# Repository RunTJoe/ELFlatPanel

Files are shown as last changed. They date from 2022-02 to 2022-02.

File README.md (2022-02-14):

# DIY Electroluminescence Flatfield Panel

## Overview

Features:

- Software controlled brightness

- Motorized telescope cover

- "Alnitak Generic Commands" compatible protocol

- 3D printed enclosure

The panel is designed for my 120mm refractor. I have mounted a 160mm EL panel into a 3D printed telescope cover. A servo motor opens and closes the cover.

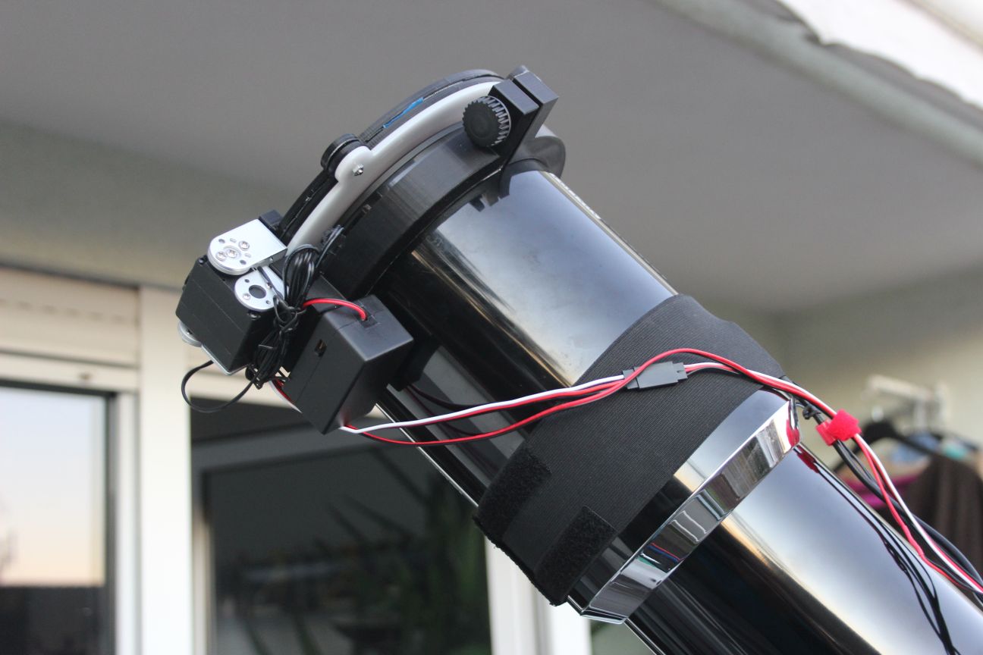
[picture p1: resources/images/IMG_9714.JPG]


Brightness and open/close operation are controlled by software using an "Alnitak Generic Commands" compatible protocol. This protocol is supported by several imaging software, I have tested operation in depth with imaging software "[Voyager](https://software.starkeeper.it/)" and briefly with "[N.I.N.A.](https://nighttime-imaging.eu/)".

Meanwhile I have successfully tested the panel for a whole night of unattended operation with temperatures below 0°C/ 32°F. During this night I shot multiple targets with different rotator angles and got the fitting flats for each rotator position. The imaging software automatically determined the correct brightness for luminance and narrowband filters and a fixed exposure time to fit my flatdark library.

## Panel

The panel is a cheap 160mm EL panel from Aliexpress. The controller is designed to be connected to a 12V inverter.

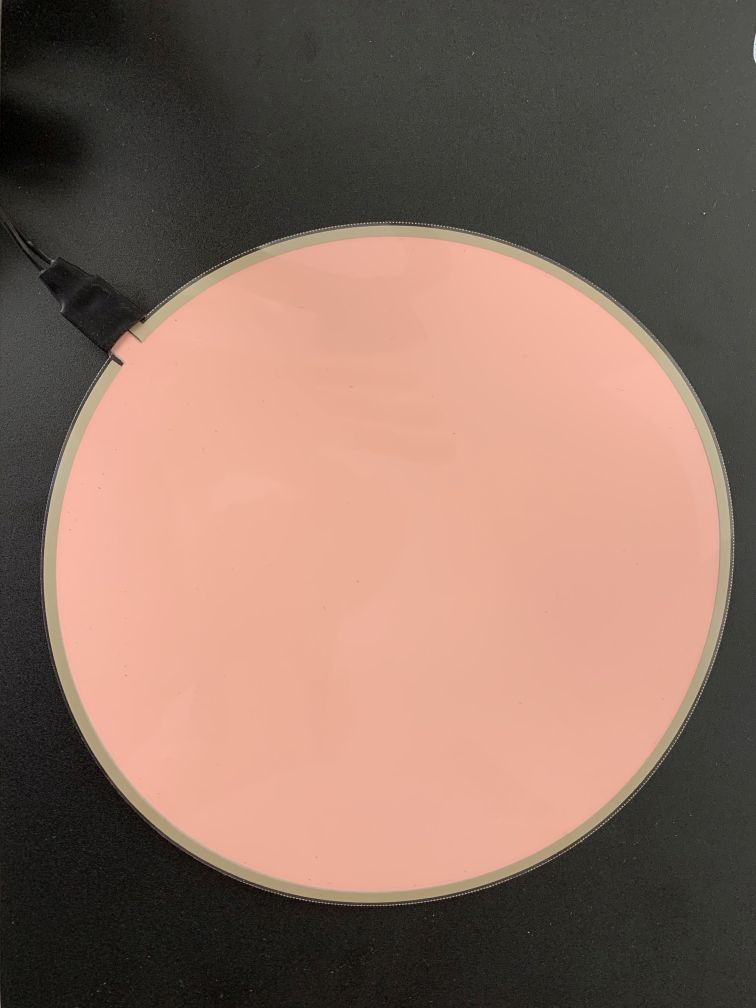
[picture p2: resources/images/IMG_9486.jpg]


## Enclosure/Mounting

The whole enclosure, servo motor attachment and telescope "tube ring" are 3D printed. I have added a laser cut acrylic diffusor plate, although I don’t know whether this necessary.

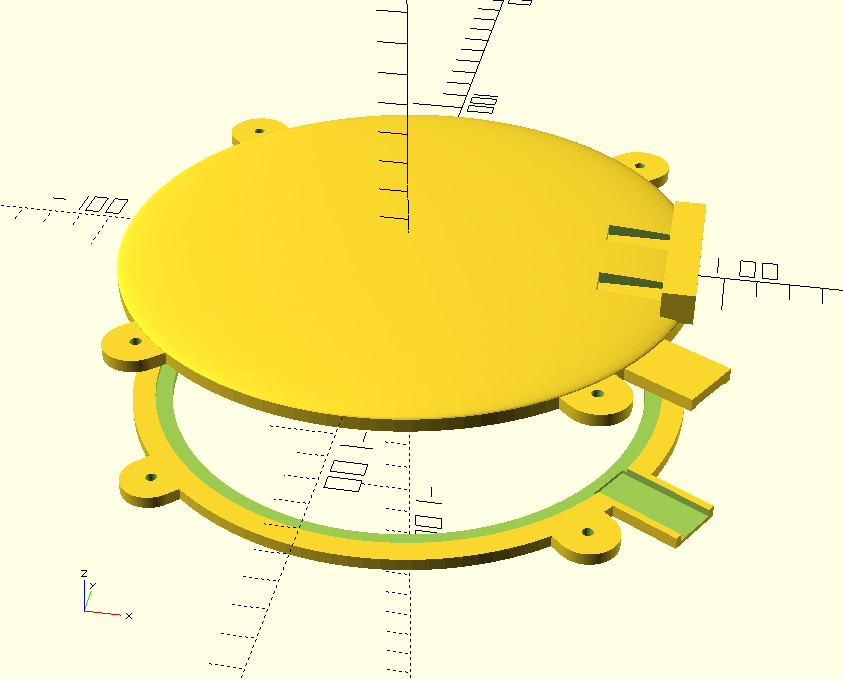
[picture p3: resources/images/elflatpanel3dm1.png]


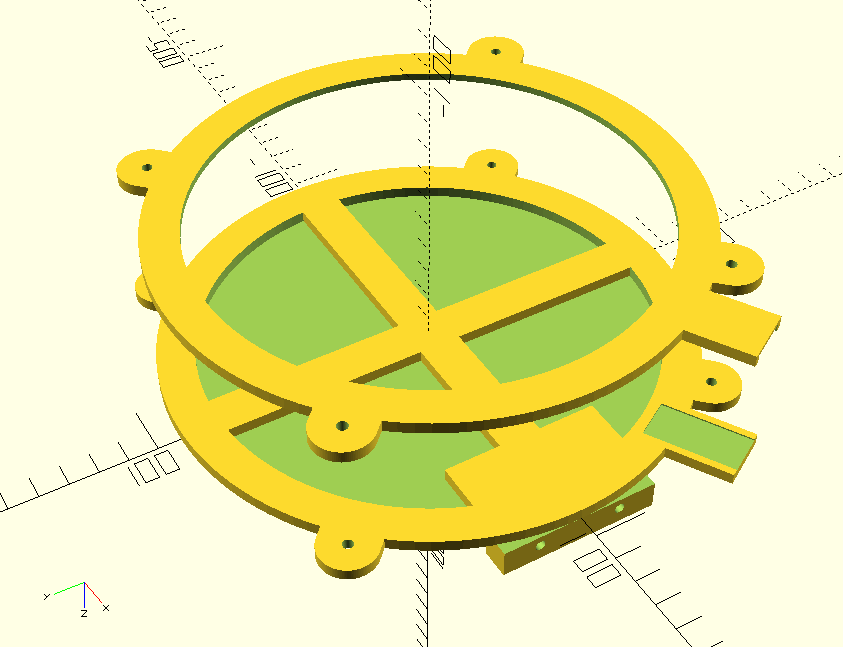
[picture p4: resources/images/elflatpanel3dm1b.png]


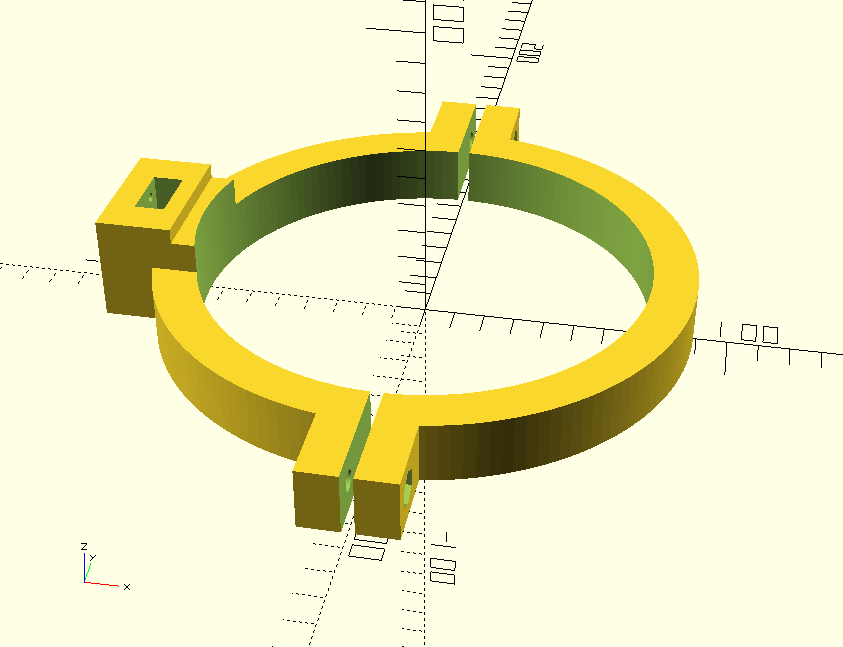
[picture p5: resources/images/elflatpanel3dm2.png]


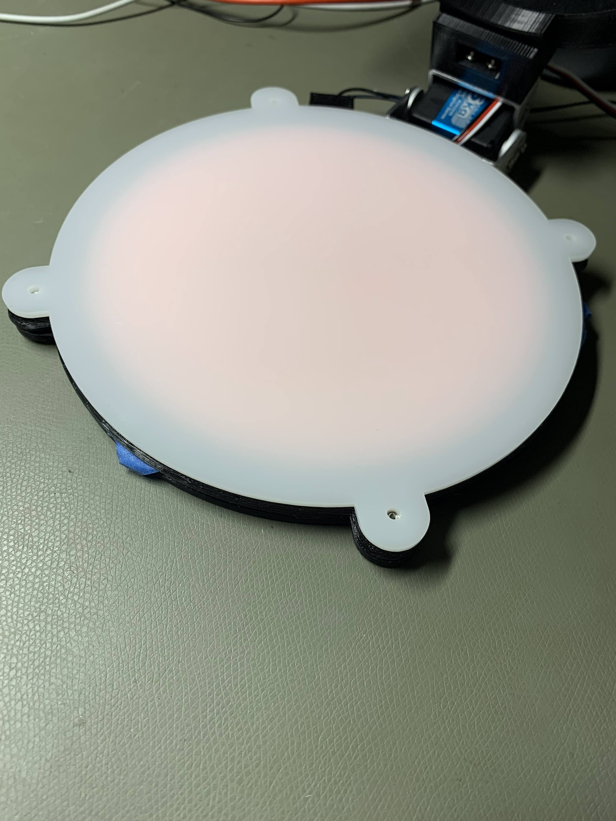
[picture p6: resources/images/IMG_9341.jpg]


## Controller

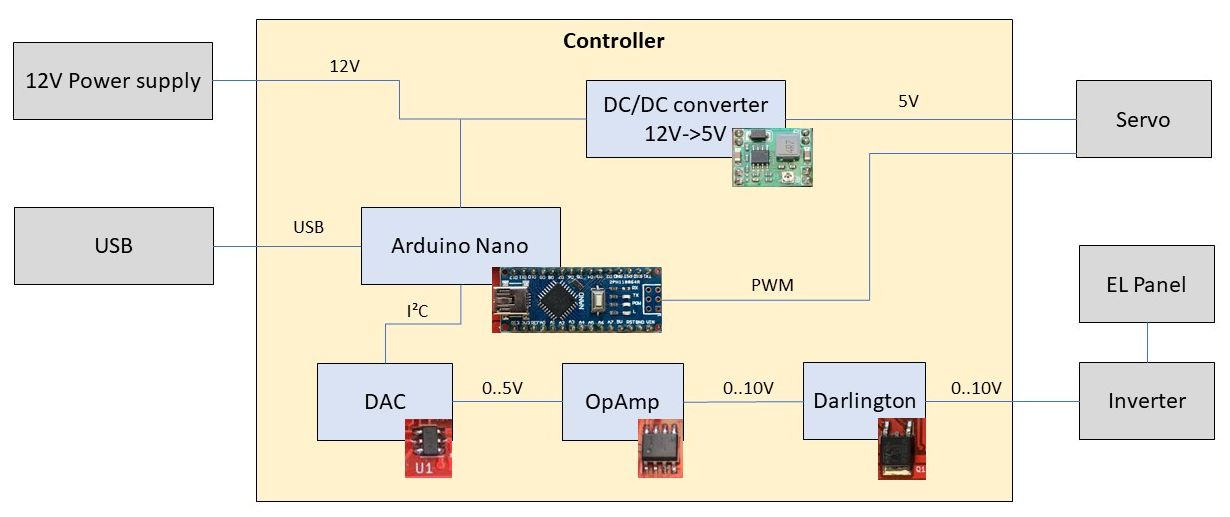
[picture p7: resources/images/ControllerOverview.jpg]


The controller is based on an Arduino Nano. The servo is controlled directly by a PWM pin of the Arduino. The inverter of the EL panel is a 12V inverter and the brightness is dimmed by reducing the inverter input voltage. For that purpose I have used an external DAC MCP4725 (the Arduino analog outputs are just PWM digital outputs) and translated the 0-5V output of this DAC via an OpAmp and a darlington transistor to 0-10V.

I have designed a PCB (using KiCAD) to fit into a very compact project box (8x5x2cm) which remains fixed on the refractor while it is stored in the telescope case. 

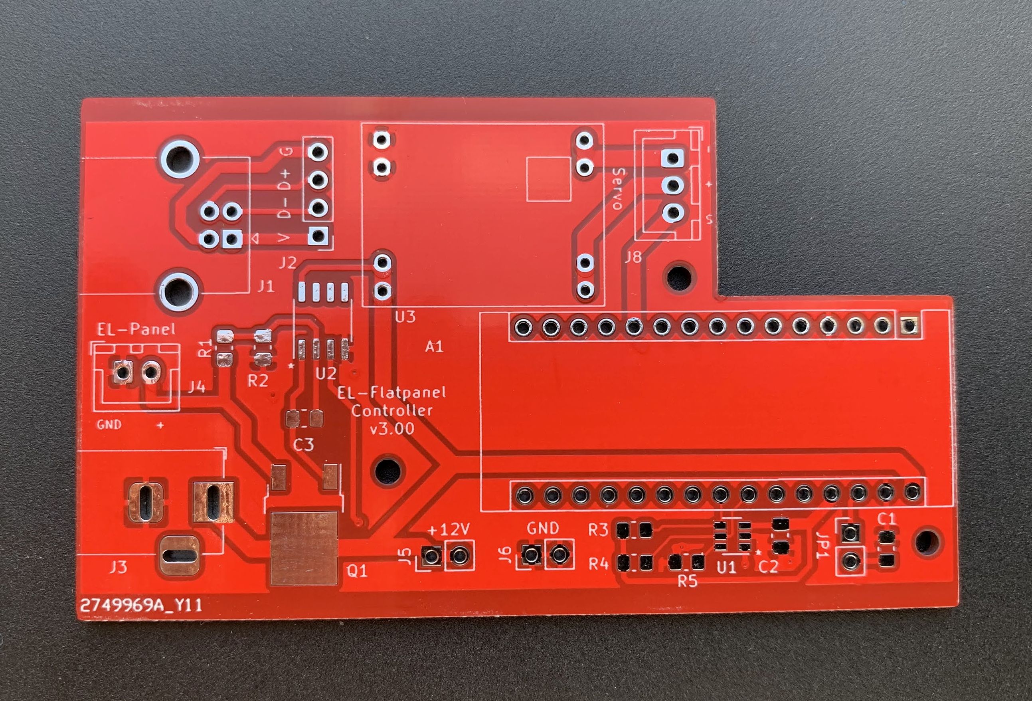
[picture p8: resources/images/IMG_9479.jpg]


By default, the Arduino resets on each connect by the USB serial port. By shorting JP1 with a jumper this reset can be disabled. This is useful if the controller is connected to software with tight timeouts. You must remove the jumper if you want to update the Arduino firmware.

Front and back plates of the box are aluminum "PCBs" produced at the same PCB manufacturer ([JLCPCB](https://jlcpcb.com/)).

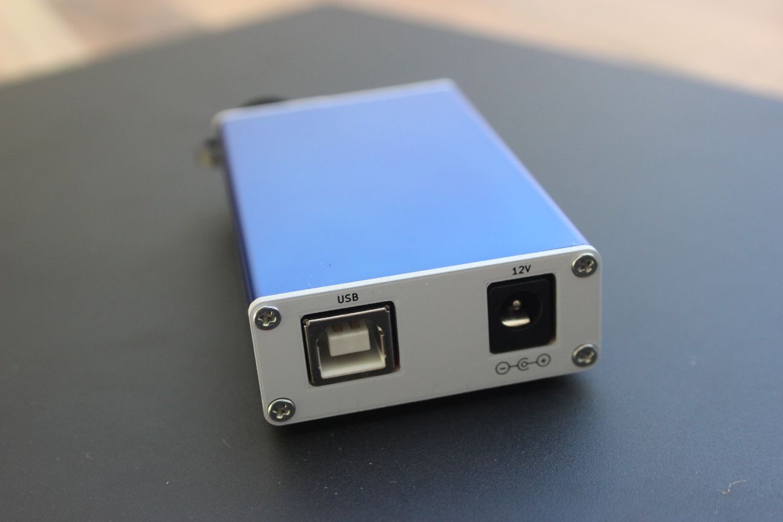
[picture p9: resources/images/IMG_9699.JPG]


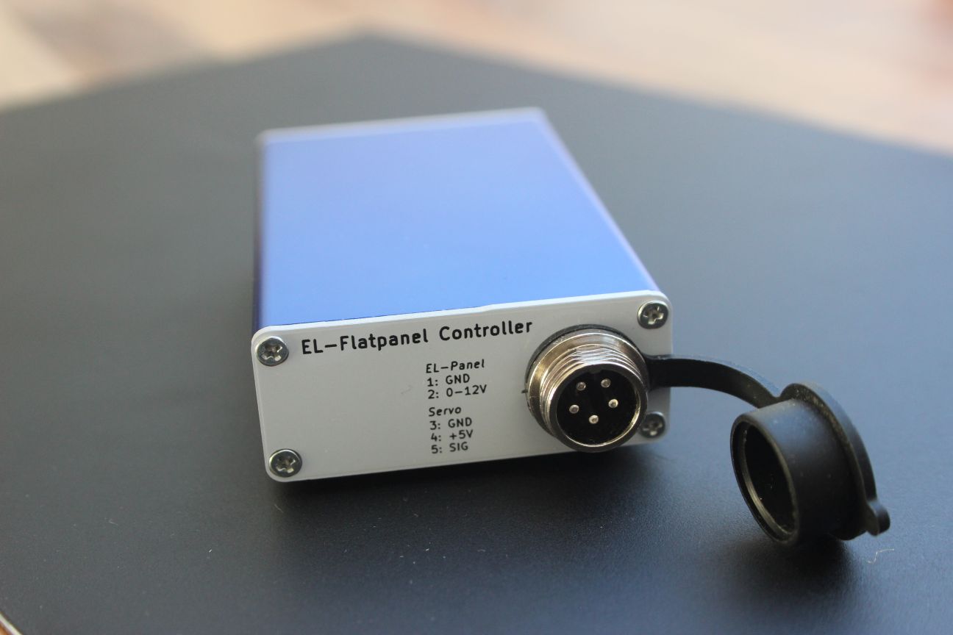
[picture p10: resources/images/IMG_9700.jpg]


**Note**: The manufacturer JLCPCB adds by default an order number on each PCB. If you spend \$1.50 more, you can choose an [option to get the PCB without the order number](https://support.jlcpcb.com/article/28-how-to-put-jlc-production-id-at-a-specified-area-on-the-pcb).

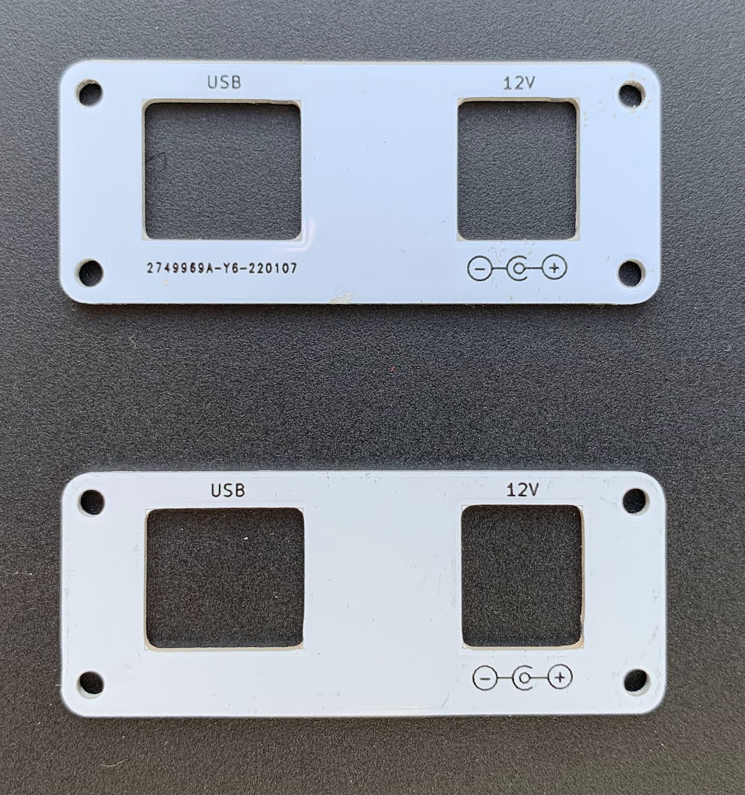
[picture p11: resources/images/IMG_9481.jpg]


The mini-USB connector of the Arduino Nano is routed to a more reliable USB-B connector. Supply voltage is the usual 12V, a DC/DC converter module on the PCB provides 5V power for the servo motor. I have bought the Arduino and DC/DC converter as complete modules, all other components are just hand soldered on my own PCB (the red PCB on the image). 

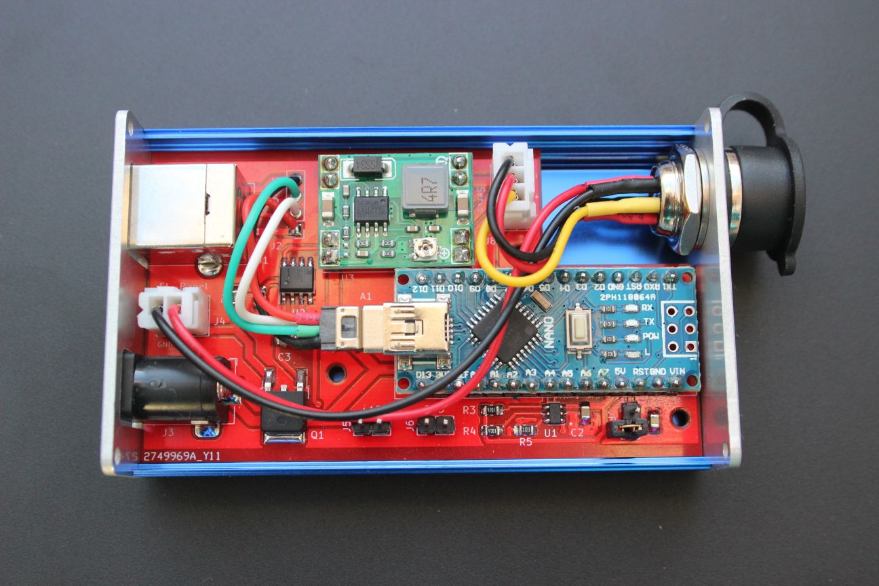
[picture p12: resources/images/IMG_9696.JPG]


**Note**: The DC/DC converter has adjustable output voltage and must be adjusted to a voltage fitting the servo (usually 5V).

## Servo

The servo is an RDS3115 with a range of 270 degrees. With my servo attachment about 225 degrees can be used.

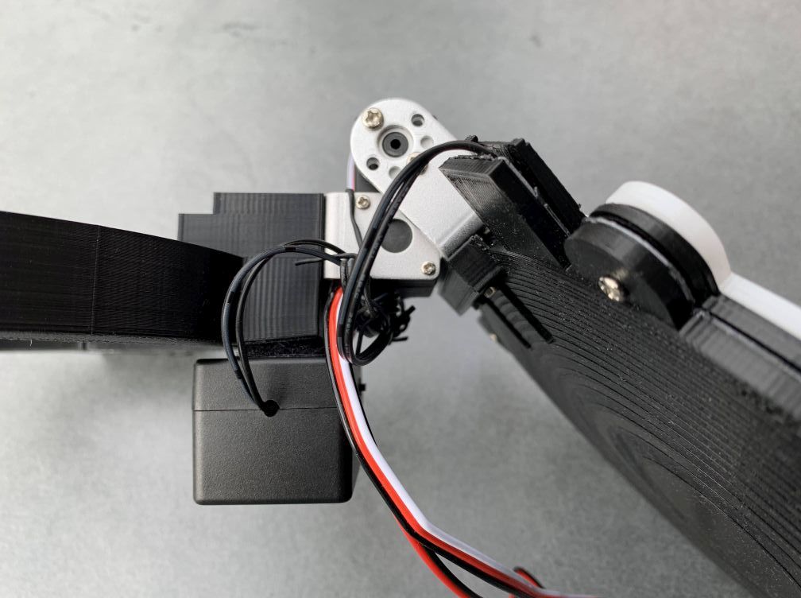
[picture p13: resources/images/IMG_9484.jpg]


The exact PWM values for opening and closing angles can be adjusted in the firmware:

```
const int SERVOPOS_CLOSE = 3;        // servo position for closed cover
const int SERVOPOS_OPEN = 158;       // servo position for open cover 
```

For easy evaluation of the proper settings, I have extended the Alnitak protocol with an additional command to set any PWM value:

Set ddd as servo PWM value:

\>Zddd*CR*

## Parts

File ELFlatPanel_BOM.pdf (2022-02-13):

Ref | Qnty | Value | Cmp name | Footprint | Description | Vendor
A1, | 1 Arduino_Nano_v3.x Arduino_Nano_v3.x Module:Arduino_Nano | Arduino Nano v3.x
C1, | | 1 10uF | CP | Capacitor_SMD:C_0805_2012Metric_Pad1.18x1.45mm_HandSolder | Polarized capacitor
C2, | | 1 0.1uF | C | Capacitor_SMD:C_0805_2012Metric_Pad1.18x1.45mm_HandSolder | Unpolarized capacitor
C3, | | 1 100pF | C | Capacitor_SMD:C_0805_2012Metric_Pad1.18x1.45mm_HandSolder | Unpolarized capacitor
J1, | | 1 USB_B | USB_B | Connector_USB:USB_B_OST_USB-B1HSxx_Horizontal | USB Type B connector
J2, | 1 Conn_01x04 | Conn_01x04 | Connector_PinHeader_2.54mm:PinHeader_1x04_P2.54mm_Vertical Generic connector, single row, 01x04, script generated (kicad-library-utils/schlib/autogen/connector/)
J3, | | 1 Barrel_Jack_Switch | Barrel_Jack_Switch | Connector_BarrelJack:BarrelJack_Horizontal | DC Barrel Jack with an internal switch
J4, | 1 Conn_01x02 | Conn_01x02 | Connector_JST:JST_XH_B2B-XH-A_1x02_P2.50mm_Vertical | Generic connector, single row, 01x02, script generated (kicad-library-utils/schlib/autogen/connector/)
J5, J6, | 2 Conn_01x02 | Conn_01x02 | Connector_PinHeader_2.54mm:PinHeader_1x02_P2.54mm_Vertical Generic connector, single row, 01x02, script generated (kicad-library-utils/schlib/autogen/connector/)
J8, | 1 Conn_01x03 | Conn_01x03 | Connector_JST:JST_XH_B3B-XH-A_1x03_P2.50mm_Vertical | Generic connector, single row, 01x03, script generated (kicad-library-utils/schlib/autogen/connector/)
JP1, | 1 Jumper | Jumper | Connector_PinHeader_2.54mm:PinHeader_1x02_P2.54mm_Vertical Jumper, normally closed
Q1, | | 1 MJD122 | TIP122 | Package_TO_SOT_SMD:TO-252-2 | 5A Ic, 100V Vce, Silicon Darlington Power NPN Transistor, TO-220
R1, R2, R3, R4, | | 4 4k7 | R | Resistor_SMD:R_0805_2012Metric_Pad1.15x1.40mm_HandSolder | Resistor
R5, | | 1 10k | R | Resistor_SMD:R_0805_2012Metric_Pad1.15x1.40mm_HandSolder | Resistor
U1, | | 1 MCP4725A0T-ECH | MCP4725xxx-xCH | Package_TO_SOT_SMD:SOT-23-6 | 12-bit Digital-to-Analog Converter, integrated EEPROM, I2C interface, SOT-23-6
U2, | | 1 LM358 | LM358 | Package_SO:SO-8_3.9x4.9mm_P1.27mm | Low-Power, Dual Operational Amplifiers, DIP-8/SOIC-8/TO-99-8
U3, | 1 MP1584ModuleDcDc MP1584ModuleDcDc ELFlatPanel:MP1584_DCDC_Module

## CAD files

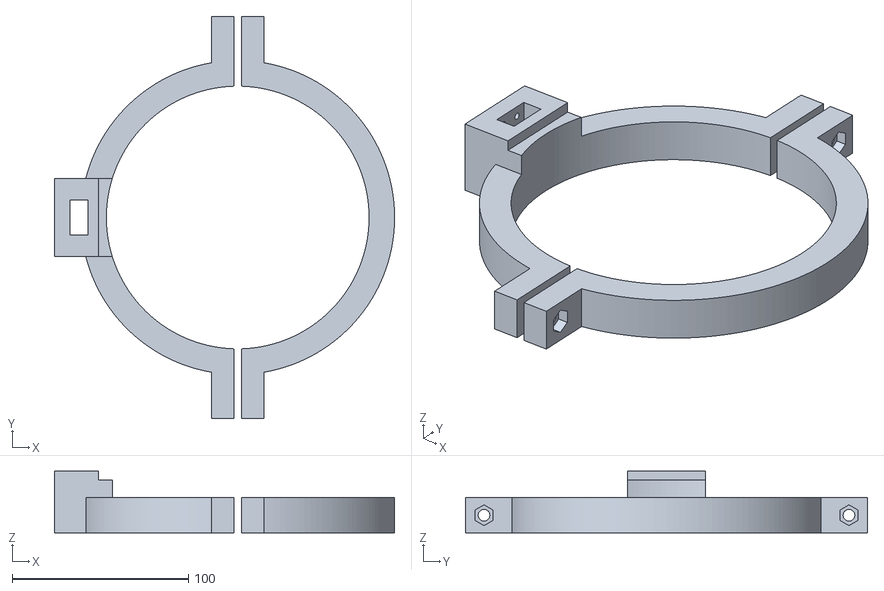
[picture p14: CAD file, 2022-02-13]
Model3D/flipflat2.stl
193.0 x 228.0 x 35.0

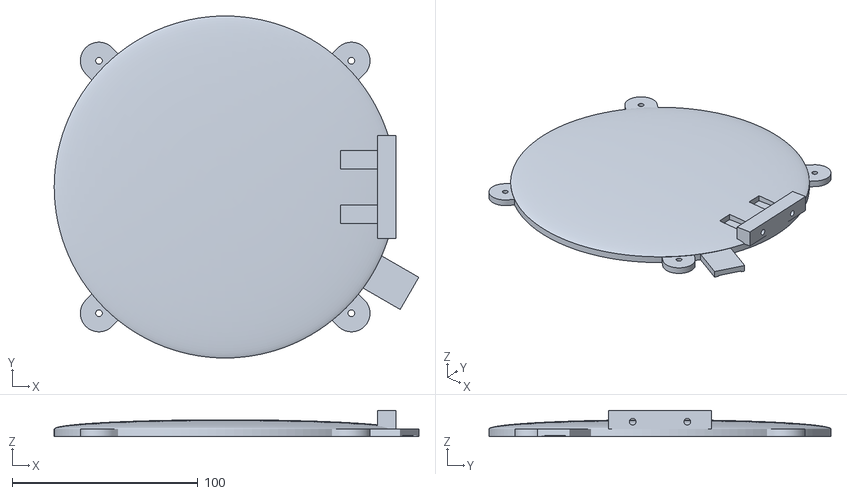
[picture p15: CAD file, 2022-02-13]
Model3D/flipflat.stl
196.2 x 184.0 x 14.0

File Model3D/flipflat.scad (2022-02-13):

// Flatpanel Version 3

  $fn=120;
  
  Tubusradius = 74;
  Panelradius = 84.5;
  Rand = 7.5;
  DickePanelFolie = 1.5;
  ServoBrakPan_d = 10;  // Dicke Block Servo-Bracket Panelanschluss
  ServoBrakPan_h = 14;  // Höhe Servo-Bracket Panelanschluss

  DickeDeckelZyl = 4;    // Dicke des Deckel-Zylinders
  BreiteAnschlBlock = 20;
  
  DickePanelRing = DickeDeckelZyl;
  
  OffsBohrServoBlock = 14.7;
  ServBlockMutterAusschnX = 20;
  ServBlockMutterAusschnY = 10;
  

module ELPanel() {
   union() {
      cylinder(h=DickePanelFolie, r=Panelradius,center=true);
      translate([Panelradius-2,-7.5,-1.8]) cube([17.2,15,3.6], center=false);
      translate([Panelradius+15.2,-7.5,-1.8]) cube([21,15,3.6], center=false);
      //translate([Panelradius-5,-6.75,-0.25]) cube([15.2,13.5,0.5], center=false);
   }
}


module AnschlBlock() {  // Halber Block fuer Panel-Anschluss
   cube([30,BreiteAnschlBlock,DickeDeckelZyl]);
}

module EinzelBohrungServoBlock() {
    rotate([0,90,0]) cylinder(h=10, r=1.8);
}

module BohrungenServoBlock() {
  translate([0,OffsBohrServoBlock,0]) EinzelBohrungServoBlock();
  translate([0,-1*OffsBohrServoBlock,0]) EinzelBohrungServoBlock();
  //translate([0,OffsBohrServoBlock,10]) EinzelBohrungServoBlock();
  //translate([0,-1*OffsBohrServoBlock,10]) EinzelBohrungServoBlock();
}

module MountPadSingle () {
    difference() {
    union() {
      translate([0,0,0]) 
         cylinder(h=DickeDeckelZyl, r=10);
      translate([-10,0,0]) 
         cube([20,10,DickeDeckelZyl]);
    }
      cylinder(h=DickeDeckelZyl, r=1.8);
    }
}

module MountPads() {
    rotate([0,0,45])
    union() {
      translate([0,Panelradius+Rand+2.5+1.55,0]) rotate([0,0,180])
         MountPadSingle();
      translate([0,-1*(Panelradius+Rand+2.5+1.55),0]) 
         MountPadSingle();
      translate([-1*(Panelradius+Rand+2.5+1.55),0,0]) rotate([0,0,-90])
         MountPadSingle();    
      translate([(Panelradius+Rand+2.5+1.55),0,0])  rotate([0,0,90]) 
         MountPadSingle();
    }    
}


// Oberteil 
union() {
  difference () {
    union () {      
        union () {
          difference () {
            union () {
              resize(newsize=[2*(Panelradius+Rand),2*(Panelradius+Rand),10]) 
                sphere(r=Panelradius+Rand);
              translate([Panelradius+Rand-(ServoBrakPan_d/2),0,(ServoBrakPan_h/2)-DickeDeckelZyl]) 
                  cube([ServoBrakPan_d,55.6,ServoBrakPan_h],true); 
            }
            translate([0,0,-1*DickeDeckelZyl]) 
              cube([2*(Panelradius+Rand)+50,2*(Panelradius+Rand),2*DickeDeckelZyl],true); // Alles mit z<0 abschneiden
          }   
          translate([0,0,-1*DickeDeckelZyl]) 
            cylinder(h=DickeDeckelZyl, r=Panelradius+Rand);
       // }
      }
      rotate([0,0,-30]) translate([Panelradius,-1*(BreiteAnschlBlock/2),-DickeDeckelZyl]) 
        AnschlBlock();
    }
    translate([Panelradius+Rand-ServBlockMutterAusschnX-ServoBrakPan_d,OffsBohrServoBlock-(ServBlockMutterAusschnY/2),0]) 
      cube([ServBlockMutterAusschnX,ServBlockMutterAusschnY,25]);
    translate([Panelradius+Rand-ServBlockMutterAusschnX-ServoBrakPan_d,-1*(OffsBohrServoBlock+(ServBlockMutterAusschnY/2)),0]) 
      cube([ServBlockMutterAusschnX,ServBlockMutterAusschnY,25]);
    translate([Panelradius+Rand-ServoBrakPan_d,0,DickeDeckelZyl]) BohrungenServoBlock();
    translate([0,0,-5.251]) rotate([0,0,-30]) ELPanel();
  
    difference () {
      translate([0,0,-1*DickeDeckelZyl]) 
        cylinder(h=DickeDeckelZyl, r=Tubusradius+5);
      translate([0,0,-0.5*DickeDeckelZyl])
        cube([15,2*(Tubusradius+5),DickeDeckelZyl],true);
      rotate([0,0,90]) translate([0,0,-0.5*DickeDeckelZyl])
        cube([15,2*(Tubusradius+5),DickeDeckelZyl],true);
    }
  }
  translate([Panelradius+Rand-ServBlockMutterAusschnX-ServoBrakPan_d-5,-27.8,-1*DickeDeckelZyl]) 
    cube([ServBlockMutterAusschnX+5,55.6,DickeDeckelZyl]);
  translate([0,0,-DickePanelRing]) MountPads();
}
  

// Unterteil
union() {  
  difference() {
    union() {
      translate([0,0,-55])
        cylinder(h=DickePanelRing, r=Panelradius+Rand, center=false);
      translate([0,0,-55])
      rotate([0,0,-30]) translate([Panelradius,-1*(BreiteAnschlBlock/2),0]) 
        AnschlBlock();  
    }
    translate([0,0,-55])
      cylinder(h=DickePanelRing, r=Tubusradius+5, center=false);
    translate([0,0,-55-(DickePanelFolie/2)+DickeDeckelZyl]) rotate([0,0,-30]) ELPanel();
  }
  translate([0,0,-55]) MountPads();
}

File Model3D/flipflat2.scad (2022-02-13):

$fn=150;
  
Tubusradius = 74;

module TubeRing(mutter = 0) {
  difference() {
    union() {
      cylinder(h=20, r=Tubusradius+15, center=false);
      translate([-15,Tubusradius,0]) cube([15,40,20]);
      translate([-15,-1*(Tubusradius+40),0]) cube([15,40,20]);
    }
    cylinder(h=20, r=Tubusradius+0.5, center=false);
    translate([-2, -1*((Tubusradius+15+40)), 0]) cube([(Tubusradius+15)+10,2*(Tubusradius+15+40),20]);   
    
    translate([-7.5,Tubusradius+15+12.5+2,10]) rotate([0,90,0]) cylinder(h=15, r=3.3, center=true);
    translate([-7.5,-1*(Tubusradius+40-12.5+2),10]) rotate([0,90,0]) cylinder(h=15, r=3.3, center=true);
    
    if (mutter) {
      translate([-15,Tubusradius+15+12.5+2,10]) rotate([0,90,0]) cylinder(h=5, r=5.9, $fn=6); 
      translate([-15,-1*(Tubusradius+40-12.5+2),10]) rotate([0,90,0]) cylinder(h=5, r=5.9, $fn=6); 
    }
  }   
}


translate([0,0,20]) rotate([0,180,0]) TubeRing(1);

difference() {
    union() {
      TubeRing();        
        translate([-1*((Tubusradius+15)+15),-22.2,0]) cube([25,44.4,35]);
        translate([-1*((Tubusradius+15)+14),-22.2,0]) cube([40,44.4,30]);
    }
  
    translate([-1*((Tubusradius+15+6)),-10,0]) cube([10,20,35]);
    translate([-1*((Tubusradius+15+6+5)),5,30]) rotate([0,90,0]) cylinder(h=10, r=1.55, center=true);
    translate([-1*((Tubusradius+15+6+5)),5,20]) rotate([0,90,0]) cylinder(h=10, r=1.55, center=true);
    translate([-1*((Tubusradius+15+6+5)),-5,30]) rotate([0,90,0]) cylinder(h=10, r=1.55, center=true);
    translate([-1*((Tubusradius+15+6+5)),-5,20]) rotate([0,90,0]) cylinder(h=10, r=1.55, center=true);    
    
    cylinder(h=30, r=Tubusradius+0.5, center=false);

}

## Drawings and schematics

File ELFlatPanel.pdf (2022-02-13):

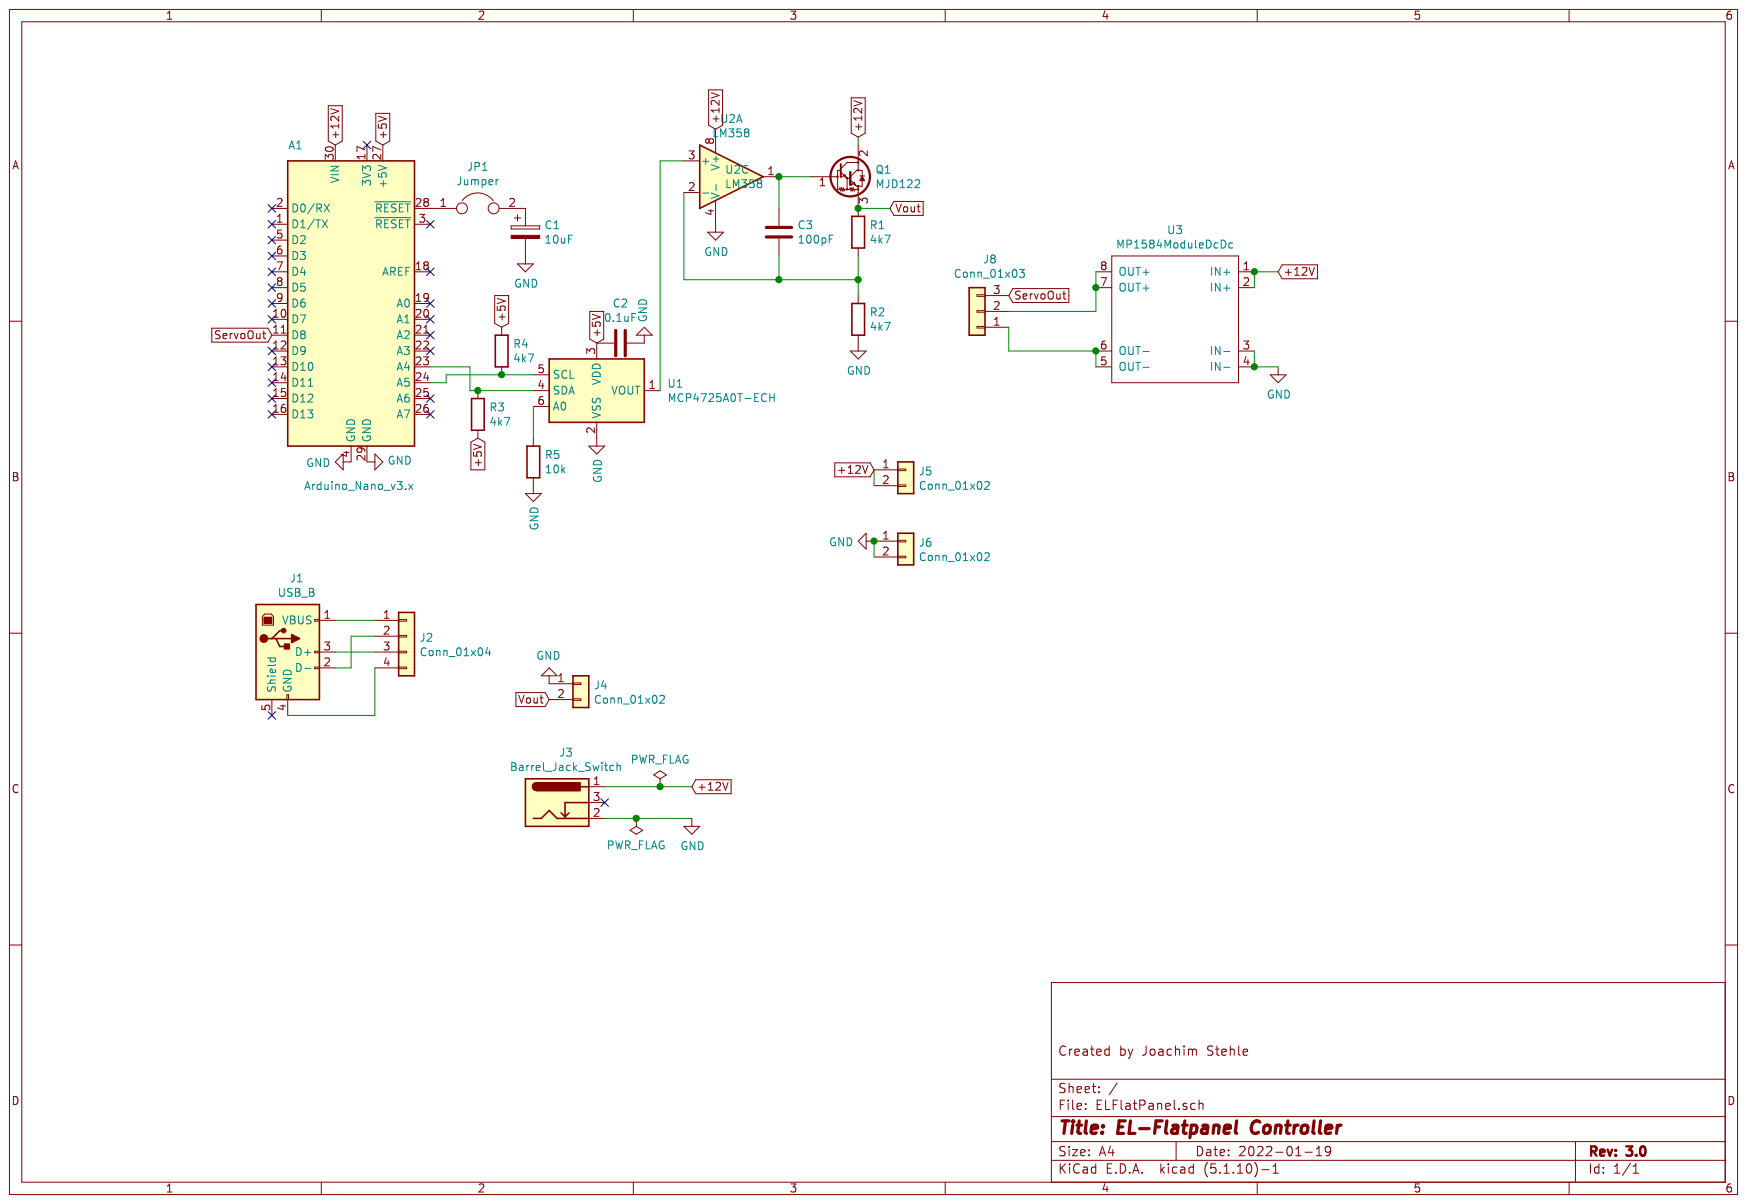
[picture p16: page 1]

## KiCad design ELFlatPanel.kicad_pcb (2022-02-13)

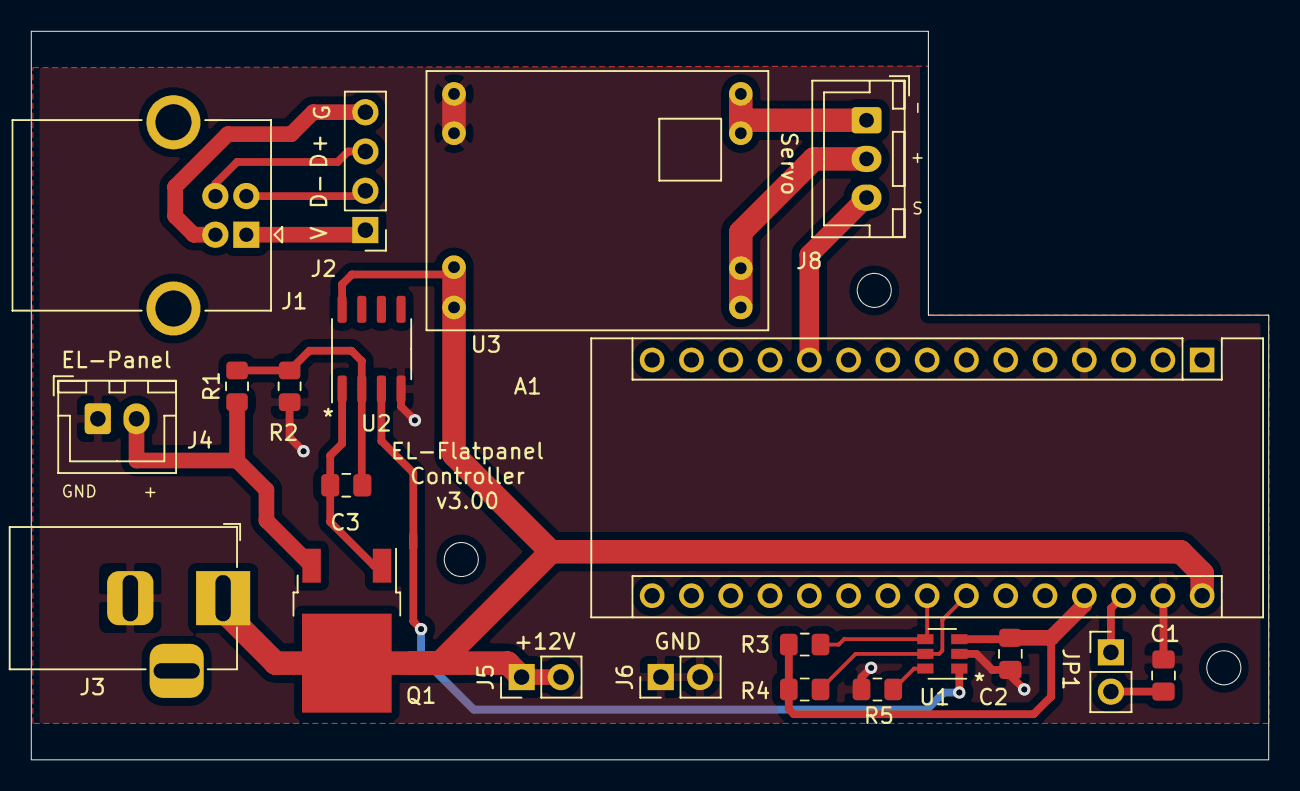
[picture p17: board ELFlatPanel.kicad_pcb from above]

Board: 2 copper layers, 80.0 x 47.1 mm, 21 parts (0 on the bottom side), 19 nets.

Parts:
A1: Arduino_Nano_v3.x; Arduino_Nano
C1: 10uF; C_0805_2012Metric_Pad1.18x1.45mm_HandSolder
C2: 0.1uF; C_0805_2012Metric_Pad1.18x1.45mm_HandSolder
C3: 100pF; C_0805_2012Metric_Pad1.18x1.45mm_HandSolder
J1: USB_B; USB_B_OST_USB-B1HSxx_Horizontal
J2: Conn_01x04; PinHeader_1x04_P2.54mm_Vertical
J3: Barrel_Jack_Switch; BarrelJack_Horizontal
J4: Conn_01x02; JST_XH_B2B-XH-A_1x02_P2.50mm_Vertical
J5, J6: Conn_01x02; PinHeader_1x02_P2.54mm_Vertical
J8: Conn_01x03; JST_XH_B3B-XH-A_1x03_P2.50mm_Vertical
JP1: Jumper; PinHeader_1x02_P2.54mm_Vertical
Q1: MJD122; TO-252-2
R1, R2, R3, R4: 4k7; R_0805_2012Metric_Pad1.15x1.40mm_HandSolder
R5: 10k; R_0805_2012Metric_Pad1.15x1.40mm_HandSolder
U1: MCP4725A0T-ECH; SOT-23-6
U2: LM358; SO-8_3.9x4.9mm_P1.27mm
U3: MP1584ModuleDcDc; MP1584_DCDC_Module

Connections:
+5V: A1.27, C2.2, R3.2, R4.1, U1.3
+12V: A1.30, J3.1, J5.1, J5.2, Q1.2, U2.8, U3.1, U3.2
GND: A1.4, A1.29, C1.2, C2.1, J3.2, J4.1, J6.1, J6.2, R2.2, R5.2, U1.2, U2.4, U3.3, U3.4
unnamed: A1.23, R3.1, U1.4
unnamed: A1.24, R4.2, U1.5
unnamed: A1.28, JP1.1
unnamed: C1.1, JP1.2
unnamed: C3.1, Q1.1, U2.1
unnamed: C3.2, R1.2, R2.1, U2.2
unnamed: J1.1, J2.1
unnamed: J1.2, J2.2
unnamed: J1.3, J2.3
unnamed: J1.4, J2.4
unnamed: J8.1, U3.5, U3.6
unnamed: J8.2, U3.7, U3.8
unnamed: R5.1, U1.6
unnamed: U1.1, U2.3
ServoOut: A1.11, J8.3
Vout: J4.2, Q1.3, R1.1

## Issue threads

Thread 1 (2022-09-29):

270 degrees and Alnitak mod

Totoleheros, 2022-09-29:
Thank you so much for sharing this super project. With a friend of mine, we have started to build the project. We are facing a minor problem: we bought 270 degree RDS3115 motors ([Link](https://fr.aliexpress.com/item/32880479517.html?spm=a2g0o.order_list.0.0.7bba5e5bi2gOYU&gatewayAdapt=glo2fra)) but we cannot achieve 270 degrees movement using your Arduino code, customized as follows:

// To be adapted
const unsigned long MOVING_TIME = 2500L;    // motor moving time (for open or close) in ms
const int SERVOPOS_CLOSE = 0;               // servo position for closed cover
const int SERVOPOS_OPEN = 270;              // servo position for open cover
const int SLOW_LOW = 30;                    // low border for slow movement
const int SLOW_HIGH = 220;                  // high border for slow movement
const int SLOW_CYCLE = 40;                  // cycle time for slow movement increment (ms)
const int FAST_CYCLE = 20;                  // cycle time for fast movement increment (ms)

The max that we can get is 250 degrees, which will be ok, but we wish to understand why the hell we do not reach the 270 degrees !

And we have a question regarding the last sentence of your README.md file:

For easy evaluation of the proper settings, I have extended the Alnitak protocol with an additional command to set any PWM value:
>ZdddCR        Set ddd as servo PWM value

Could you explain us if we have to implement this additional command and how this can be done please?

Many thanks in advance!

PS: these questions were posted also on the CloudyNight forum, sorry for the duplicate request.

RunTJoe, 2022-11-03:
As already replied on the CloudyNight forum, here the same reply:

I guess the pulse length required for your servo motor does not match the default pulse length of the Arduino servo library. You can try to modify the default values by passing 2 additional arguments for minimum and maximum pulse length at servo initialization:

`line 302:      panelServo.attach(SERVO_PIN, min, max);`

See [https://www.arduino.cc/reference/en/libraries/servo/attach/](https://www.arduino.cc/reference/en/libraries/servo/attach/) for more information.

You can send the >Zddd command (and all other commands) by typing it into the serial monitor of the Arduino IDE while connected to the Arduino (or use any other serial terminal of your choice). E.g typing >Z042<CR> will move the servo to position 42 (degrees).

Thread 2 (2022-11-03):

EL Flat Panel failed to recognize change when Parked or Unparked

LauDeash, 2022-11-03:
Hi @RunTJoe,

Huge thanks for sharing this solution flats solution.  A buddy of mine and I are right at the finish line building this, but we're having a small issue.  When we run the Indi flip_flat drive in Ekos I can manually unpark and park the cap but the buttons don't change to green respectively and the status light stays red.   It's all good if I'm going to babysit the rig that night, but it falls apart when I want to introduce automation, like the scheduler. Since it's not recognizing it's actually unparked when it is it causes it to abort the job.  I can't help but feel like it might be driver related and I've posted on the indilib forums, but I thought I'd reach out to you too.  See if you have any suggestions.  Thanks for any help you can offer and let me know what I can provide to help out.

RunTJoe, 2022-11-03:
Hi,
although I'm no expert on Indi software, let's try to find the issue.

First, to ensure that I understand the problem (sorry - I'm no native speaker...): Basically the cap status (open or closed) is not displayed in your software? Is the light status (on or off) displayed correctly?

I have just checked the software with N.I.N.A. and it displays the correct cover state. So basically the firmware seems to work correctly, at least for N.I.N.A.

Then I have then tried to look at the indi driver source code (do you know whether [https://github.com/indilib/indi/blob/master/drivers/auxiliary/flip_flat.cpp](https://github.com/indilib/indi/blob/master/drivers/auxiliary/flip_flat.cpp) is the correct driver?) to see what the driver is expecting.

Maybe I have an idea: There is a strange issue with the Alnitak protocol specification, you can find (at least) 2 different versions. The main difference is that the spec dated "1/11/09" states that the unused characters in the responses from the panel are "0" (the digit zero), but according to the spec dated "6/12/2017" these characters shall be "O" (the letter O).

This seems to cause confusion; see a code snippet from N.I.N.A.:
`if (response.Substring(4, 3).Equals("OOO")) return true;`

and one from indi flip-flat driver:
`snprintf(expectedResponse, FLAT_RES, "*C%02d000", productID);
 if (strcmp(response, expectedResponse) == 0)`

My Arduino firmware accepts both characters as input, but outputs with "O"s (not 0s). Maybe you can replace the "O"s in line 115 to 117 of  the .ino file by "0"s, upload the new firmware to the Arduino and try again.

Please let me know whether this helps, I'll try to support finding the issue.

LauDeash, 2022-11-04:
@RunTJoe,

Thanks for such a quick reply. Yes, I believe that is the right driver at least it’s the one I’ve been looking through. I’ll make those changes and let you know how it turns out.

LauDeash, 2022-11-04:
@RunTJoe,

That was it!  Thanks so much for the help.

RunTJoe, 2022-11-05:
> @RunTJoe,
>
> That was it! Thanks so much for the help.

Thank you for reporting this problem. I have meanwhile opened an issue ticket for the INDI driver.

Closed 2022-11-04.

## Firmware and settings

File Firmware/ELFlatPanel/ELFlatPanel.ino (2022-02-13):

#include <Adafruit_MCP4725.h>
#include <Servo.h>

Servo panelServo;
Adafruit_MCP4725 dac;

enum devices
{
  FLAT_MAN_L = 10,
  FLAT_MAN_XL = 15,
  FLAT_MAN = 19,
  FLIP_FLAT = 99
};

enum motorStates
{
  MS_STOPPED = 0,
  MS_RUNNING
};

enum lightStates
{
  LS_OFF = 0,
  LS_ON
};

enum coverStates
{
  CS_UNKNOWN = 0,
  CS_CLOSED,
  CS_OPEN,
  CS_TIMEOUT
};


// To be adapted
const unsigned long MOVING_TIME = 2500L;    // motor moving time (for open or close) in ms

const int SERVOPOS_CLOSE = 3;               // servo position for closed cover
const int SERVOPOS_OPEN = 158;              // servo position for open cover

const int SLOW_LOW = 30;                    // low border for slow movement
const int SLOW_HIGH = 130;                  // high border for slow movement
const int SLOW_CYCLE = 40;                  // cycle time for slow movement increment (ms)
const int FAST_CYCLE = 20;                  // cycle time for fast movement increment (ms)

const int FIRMWARE_VERSION = 3;             // firmware version

const int SERVO_PIN = 8;                    // Servo pin for PWM signal


// No adaptations necessary
//unsigned long movingEndTime = 0;            // timestamp until motor moving is reported
const int ARG_OOO = 1000;                   // reply with argument OOO

int charIdx = 0;  // index of last received character in message buffer
int argVal;       // value of received message argument
char currCmd;     // current command character of received message
unsigned long nextCheck = 0;   // timestamp for next servo movement check

motorStates currMotorState = MS_STOPPED;    // current motor state
lightStates currLightState = LS_OFF;        // current light state
coverStates currCoverState = CS_OPEN;       // current cover state
unsigned int currBrightness = 128;          // current set brightness (0..255, might be overruled by light state)
int targetServoPos = SERVOPOS_CLOSE;        // target servo position

// Set DAC value for panel brightness
void SetDAC(unsigned int val) {
  dac.setVoltage((uint16_t)(val * 16), false); // convert to 12 bit value
}


void HandleServo() {
  int currServoPos;

  if (millis() >= nextCheck) {   // time for next movement?
    currServoPos = panelServo.read();
    if (currServoPos != targetServoPos) {   // adjust to target position by 1
      if (currServoPos < targetServoPos) {
        currServoPos += 1;
      }
      else {
        currServoPos -= 1;
      }
    }
    panelServo.write(currServoPos);  // move servo
    if ((currServoPos < SLOW_LOW) || (currServoPos > SLOW_HIGH)) {   // calculate time for next movement
      nextCheck = millis() + SLOW_CYCLE;
    }
    else {
      nextCheck = millis() + FAST_CYCLE;
    }
  }
}


// Send reply, cmd=command character, arg=argument value or >10000 for OOO (NOT 000!)
void Reply(char cmd, int arg) {
  char msgBuf[9];

  msgBuf[0] = '*';
  msgBuf[1] = cmd;
  msgBuf[2] = '9';   // Flip-flat device
  msgBuf[3] = '9';
  if (arg < ARG_OOO) {    // argument is a value 0..999
    int a1 = arg % 10;
    arg = (arg - a1) / 10;
    int a10 = arg % 10;
    arg = (arg - a10) / 10;
    msgBuf[4] = (char)arg + '0';
    msgBuf[5] = (char)a10 + '0';
    msgBuf[6] = (char)a1 + '0';
  }
  else {  // argument is OOO (NOT 000!)
    msgBuf[4] = 'O';
    msgBuf[5] = 'O';
    msgBuf[6] = 'O';

  }
  msgBuf[7] = (char)0x0A;
  msgBuf[8] = 0;
  Serial.print(msgBuf);
}

// Ping
void CmdPing() {
  Reply('P', ARG_OOO);
}

// Open cover
void CmdOpen() {
  currCoverState = CS_OPEN;
  targetServoPos = SERVOPOS_OPEN;
  nextCheck = millis() + SLOW_CYCLE;
  Reply('O', ARG_OOO);
}

// Close cover
void CmdClose() {
  currCoverState = CS_CLOSED;
  targetServoPos = SERVOPOS_CLOSE;
  nextCheck = millis() + SLOW_CYCLE;
  Reply('C', ARG_OOO);
}

// Switch light on (with set brightness)
void CmdLightOn() {
  currLightState = LS_ON;
  SetDAC(currBrightness);
  Reply('L', ARG_OOO);
}

// Switch light off (but preserve brightness)
void CmdLightOff() {
  currLightState = LS_OFF;
  SetDAC(0);
  Reply('D', ARG_OOO);
}

// Set brightness
void CmdSetBrightness(int val) {
  currBrightness = val;
  if (currLightState == LS_ON) {
    SetDAC(currBrightness);
  }
  Reply('B', val);
}

// Set servo position (this is an additional command, not covered by the default protocol)
void CmdServoPos(int val) {
  panelServo.write(val);
  Reply('Z', val);
}

// Get current brightness
void CmdGetBrightness() {
  Reply('J', currBrightness);
}

// Get state
void CmdGetState() {
  int st;

  if (panelServo.read() == targetServoPos) { // not moving, report no movement and cover state
    st = (100 * currMotorState) + (10 * currLightState) + currCoverState;
  } else { // moving, report movement and unknown cover stte
    st = (100 * MS_RUNNING) + (10 * currLightState) + CS_UNKNOWN;
  }
  Reply('S', st);
}

// Get firmware version
void CmdGetVersion() {
  Reply('V', FIRMWARE_VERSION);
}

// poll UART and process received characters
void CheckUART() {
  if (Serial.available() > 0) {
    char inChar = Serial.read();

    switch (charIdx) {
      case 0:   // first char
        if (inChar == '>') {
          charIdx++;
          argVal = 0;  // clear argument value
        }
        break;
      case 1:   // 2nd char = command
        switch (inChar) {
          // supported command characters
          case 'P':
          case 'O':
          case 'C':
          case 'L':
          case 'D':
          case 'B':
          case 'J':
          case 'S':
          case 'V':
          case 'Z':
            currCmd = inChar;
            charIdx++;
            break;
          default:  // unknown command, discard all
            charIdx = 0;
            break;
        }
        break;
      case 2:   // 3.-5. char = arg
      case 3:   // 3.-5. char = arg
      case 4:   // 3.-5. char = arg
        if ((currCmd != 'B') && (currCmd != 'Z')) {  // the only commands with numerical arguments
          // no numerical argument expected
          if ((inChar == '0') || (inChar == 'O')) {
            charIdx++;
          }
          else {
            charIdx = 0;
          }
        }
        else {
          // numerical argument expected
          if (inChar == 'O') {
            inChar = '0';
          }
          if ((inChar >= '0') && (inChar <= '9')) {
            argVal = (10 * argVal) + (inChar - '0');
            charIdx++;
          }
          else {
            charIdx = 0;
          }
        }
        break;
      case 5:   // 6. char = CR
        charIdx = 0;
        if ((inChar == '\n') || (inChar == 0x0d)) {
          switch (currCmd) {
            case 'P':
              CmdPing();
              break;
            case 'O':
              CmdOpen();
              break;
            case 'C':
              CmdClose();
              break;
            case 'L':
              CmdLightOn();
              break;
            case 'D':
              CmdLightOff();
              break;
            case 'B':
              CmdSetBrightness(argVal);
              break;
            case 'J':
              CmdGetBrightness();
              break;
            case 'S':
              CmdGetState();
              break;
            case 'V':
              CmdGetVersion();
              break;
            case 'Z':
              CmdServoPos(argVal);
              break;

          }
          break;
        }
        break;
    }
  }
}


void setup() {
  dac.begin(0x60);                   // Address for MCP4725A0
  panelServo.attach(SERVO_PIN);
  SetDAC(0);                         // start with light off
  currCoverState = CS_CLOSED;
  panelServo.write(SERVOPOS_CLOSE);  // start with closed cover
  Serial.begin(9600);
}


void loop() {
  CheckUART();   // poll UART
  HandleServo();
}

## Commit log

2022-02-14 Updated servo section
2022-02-17 Added front and back panel files
    [ELPanelBack-B_Cu.gbl, ELPanelBack-B_Mask.gbs, ELPanelBack-B_Paste.gbp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]
